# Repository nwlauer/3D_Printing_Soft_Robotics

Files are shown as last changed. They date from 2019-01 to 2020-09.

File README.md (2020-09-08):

# 3D Printing Soft Robotics

  This project revolves mostly around the fabrication of a soft robotic system out of a flexible filament that requires no post processing after printing. Additionally, a new design is constructed for a worm-like robot and accompanying control system.
  
   [Instructable](http://www.instructables.com/id/How-to-Make-a-Robotic-Worm/)
  
### Credit to Others Doing similar projects

 / [Mikey77 Instructables](http://www.instructables.com/member/mikey77/)
 / [Whitesides Research Group](http://gmwgroup.harvard.edu/research/index.php?page=23)
 / [Umburry](https://umburry.com/)
 /

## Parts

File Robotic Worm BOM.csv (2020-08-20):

Description/ID | Quantity | Qty_Unit | Manufacturer | Product No. | Source Link | Unit Cost | Notes | Type
Arduino Uno R3 | 1 | - | Elegoo | EL-CB-001 | https://www.amazon.com/ELEGOO-Board-ATmega328P-ATMEGA16U2-Compliant/dp/B01EWOE0UU | $12.98 | - | Electronic
NinjaFlex | 25 | grams | NinjaTek | - | https://www.amazon.com/NinjaTek-3DNF08117505-NinjaFlex-Filament-TPE-5kg/dp/B00J12HGDW | $0.09 | If using alternatives try to get one with similar elongation and shore hardness | Hardware&Materials
PVA | 25 | grams | SainSmart | - | https://www.amazon.com/gp/product/B00SSXAET8/ref=ppx_yo_dt_b_asin_title_o08_s00?ie=UTF8&psc=1 | $0.06 | Any Brand is fine | Hardware&Materials
2mm ID x 4mm OD Silicone Tubing | 5 | ft | Generic | - | https://www.amazon.com/DERPIPE-Silicone-Tubing-Flexible-Homebrewing/dp/B07PZT7FC7 | $0.70 | - | Hardware&Materials
4mm ID x 6mm OD Silicone Tubing | 1 | ft | Generic | - | https://www.amazon.com/dp/B08BR8MQSR | $1.20 | - | Hardware&Materials
12V Mini Diaphragm Pump | 1 | - | Parker/Hargraves | C 183-22-01 | https://www.ebay.com/itm/Mini-Diaphragm-single-head-Air-And-Gas-Hargraves-Pump-2-5L-min-12VDC/301748351096 | $22.49 | Ubiquitous on the secondary market look for deals. Similar pumps can be used in place. | Electronic
6 V 2 position 3 way mini solenoid valve | 6 |  | Zonhen | ZHV-0519 | https://www.ebay.com/itm/DC-5V-6V-2-Position-3-Way-Micro-Mini-Electric-Solenoid-Valve-for-Gas-Air-Pump/263807376340 | $2.45 | Ubiquitous on secondary market, does not have to be Zonhen brand. Usually marketed for use in eye massagers. | Electronic
12V 2A Power Supply | 1 | - | Generic | - | https://www.amazon.com/100-240V-Transformers-Switching-Applications-Connectors/dp/B077PW5JC3 | $5.00 | - | Electronic
LM2596 adjustable buck converter module | 1 | - | Generic | - | https://www.amazon.com/MCIGICM-step-down-Converter-3-0-40V-1-5-35V/dp/B06XZ1DKF2 | $2.00 | - | Electronic
1k Ohm Resistor | 7 | - | Generic | - |  | $0.01 | - | Electronic
NPN Amplifier Transistor | 6 | - | Generic | BC337 | https://www.sparkfun.com/products/13689 | $0.50 | - | Electronic
Darlington Transistor | 1 | - | Generic | TIP 120 | https://www.amazon.com/TIP120-Darlington-Transistor-Arduino-Diodes/dp/B00FVLGYEY | $1.00 | - | Electronic
Clamping Diodes | 7 | - | Generic | 1N4007 | https://www.amazon.com/ILS-Pieces-Rectifier-Component-Projects/dp/B07PXV4F2C?s=electronics | $0.01 | Can use 1N4001 and up | Electronic
XH-2A Connectors | 6 | - | Generic | - | https://www.amazon.com/IZOKEE-460pcs-Connector-Housing-Terminal/dp/B0791DJMW9?s=electronics | $0.02 | Optional for connecting the solenoid valves to the circuit | Electronic
XH-4A Connector | 1 | - | Generic | - | https://www.amazon.com/IZOKEE-460pcs-Connector-Housing-Terminal/dp/B0791DJMW9?s=electronics | $0.02 | Optional for connecting the pump | Electronic
No Residue Tap | 1 | ft | Generic | - | - | $1.00 | Any kind will do, I used Kapton | Hardware&Materials
Small Zip Ties | 6 | - | Generic | - | https://www.amazon.com/TR-Industrial-TR88301-Multi-Purpose-Cable/dp/B01018DB2E?s=electronics | $0.50 | Less then 2mm width works best | Hardware&Materials
Vinyl, Fabric & Plastic Flexible Adhesive | 2 | Ounce | Loctite | 1360694 | https://www.amazon.com/Loctite-Plastic-Adhesive-1-Ounce-1360694/dp/B001F7E9VI | $2.94 | - | Hardware&Materials
Jumper Wires | 40 | - | - | - | - | $5.00 | For Breadboarding or proto-boarding | Hardware&Materials
3D Printer | 1 | - | - | - | - | - | Must be able to print NinjaFlex | Tools
Wire Cutters and Strippers | - | - | - | - | - | - | - | Tools
Soldering Iron and Solder | - | - | - | - | - | - | Optional | Tools
Breadboard | - | - | - | - | - | - | - | Tools
Straight Pick | - | - | - | - | - | - | - | Tools

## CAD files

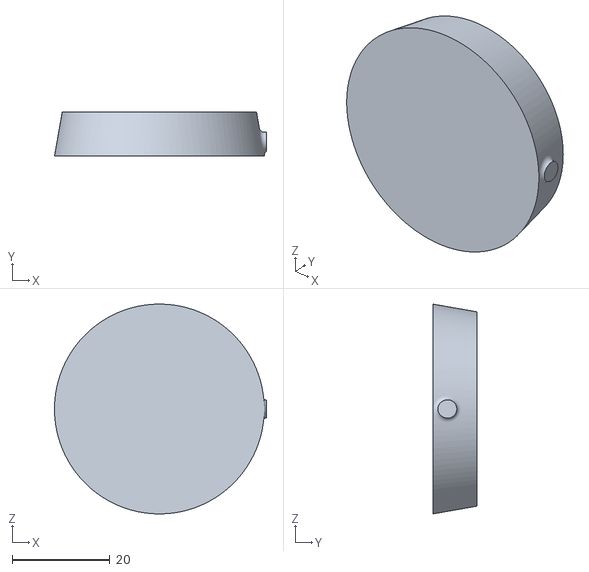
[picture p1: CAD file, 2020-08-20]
support-insert-01-offset.stl
43.4 x 9.00 x 42.9

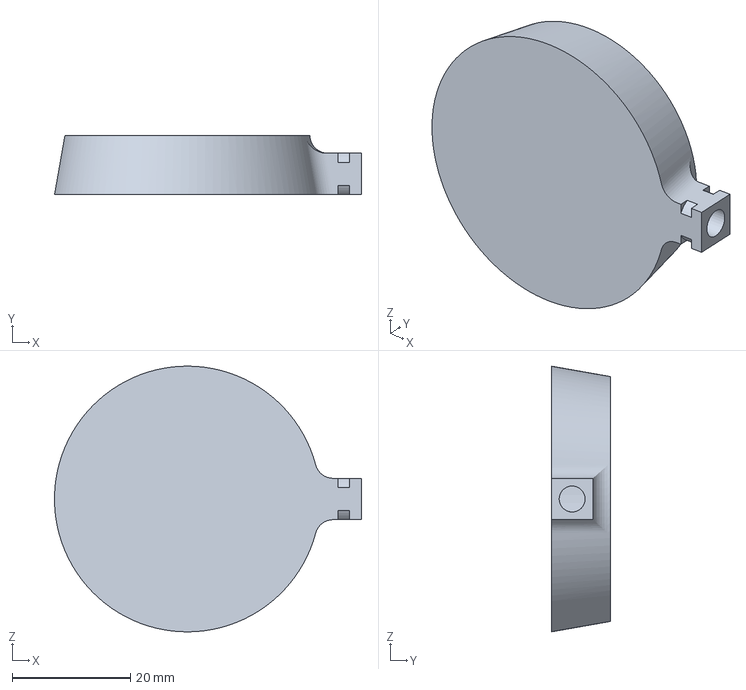
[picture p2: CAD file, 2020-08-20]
amf_file_for_mk2s (2).amf
52.0 x 10.0 x 45.0 mm

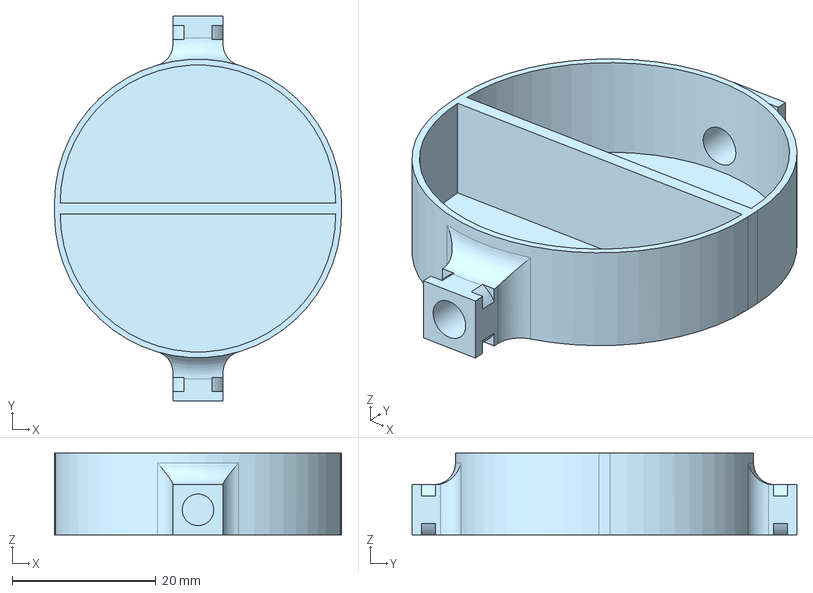
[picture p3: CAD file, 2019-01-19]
Pillow Actuator Bottom.step
40.0 x 53.6 x 11.4 mm

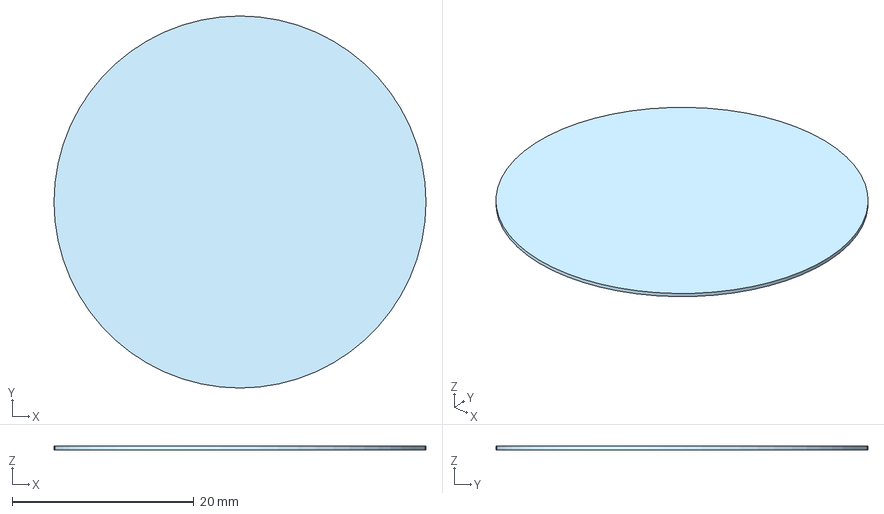
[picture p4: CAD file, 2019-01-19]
Pillow Actuator Top.step
41.0 x 41.0 x 0.4 mm

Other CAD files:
pillow-actuator-v2 (1).stl
Pillow Actuator Bottom.stl
Pillow Actuator Top.stl
pillow-actuator-v2.f3d

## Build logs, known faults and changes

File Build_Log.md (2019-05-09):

### Progress

(Jan. 15th, 2019)

It has been a while since I did an update, quite a bit has happened.

I decided to stick with the soldering iron method of creating the actuator for prototyping, in the future if it works I would like to work on creating a tool to do this with geometry to melt the specific locations of the actuator. 

Working on better settings for the top portion I found that while the rectilinear infill had the tendency to have gaps seen below, even when the outline overlap setting was increased. 

Rect

When doing infill there is a minimum line length for filling the part, the default for my printer in simplify3d was 2 mm. The circular geometry there is a line length less than 2 mm at the edges of the circle, the obvious solution would be to decrease this number until you get a solid infill. I, however, I found a better solution to be switching to a concentric infill which eliminates the issue at the edge of the circle and moves it to the center where the concentric circle to fill the center has a circumference less than 2mm, however I found that since I was over extruding and had the nozzle down further than normal it would completely fill in the center. The results of this change are bellow.

Conc

A new issue arises when the print finished, and a blob would be left in the center and the nozzle would smear over the top of the part when returning to its home position. I solved this adding some code to the end script to retract some and lift the z 10 mm. 

```
G92 E0 ; reset extruder distance
G1 E-1 F500 ; Retract 1 mm
G92 Z0 ; Relative Position Z
G1 Z10 ; Raise Z 10 mm
```

I have included my FFF process settings in the project folder for reference.

I used Loctite flexible adhesive to bond together the actuators. I only realized after that the location of the adhered portion should be closer to the center of the actuator so there can be the maximum amount of movement upon actuation.

PartialBuild

Additionally, I got two mini pumps from eBay, they are parker BLDC diaphragm pumps with feedback. Unfortunately, I accidentally shorted out one hooking it up to the power supply since I was using exposed alligator clips, I am now only using the covered type to avoid this again. I have a metro express board and some circuit python code to feed a PWM signal to the speed control pin on the motor but want to wait until I order another one before I try it, so I always have one working in reserve.

```
import board
import pulseio
from analogio import AnalogIn

analog_in = AnalogIn(board.A1) #Initialize AnalogIn
 
def duty_cycle_value(pin): #Get data from potentiometer
    return pin.value

pump = pulseio.PWMOut(board.D13, frequency=15000, duty_cycle=0) # Initialize Pump PWM. Frequency from pump data sheet

while True:
    pump.duty_cycle = duty_cycle_value(analog_in) # Loop PWM signal with duty cycle defined by pot value
```

Next, I want to design a manifold and order some solenoid valves for control.

(Sept. 18th, 2018)

I worked a bit on a new actuator design for a eventual soft robotic worm design I am working on. The design was a pillow type actuator as seen below. 

[Onshape Design](https://cad.onshape.com/documents/3c669edf96e152dec33955a7/w/b0888245c5fd9d2512150394/e/fc91afc5c4801dd98c8136da)

The first print failed due to the flexible filament not being able to bridge the distance across the actuator. This print did however show a strong bottom layer. 

FirstTry

FirstTry2

Instead of dialing in speeds and temperature to possibly allow the required bridging, I moved forward to the next design which split the actuator into two halves and also adjusted the size of the tubing hole as the previous version was a bit too small. The resulting design and print is seen below.

SecondTry1

SecondTry2

The print failed much like the one before but to a lesser extent. The higher temperature resulted in some more heavy stringing however this stinging makes me think that maybe running the top layer at travel speeds might produce better results, never the less I think adding two additional layers on top should produce a airtight top. 

After seeing the failed prints before which were just the bottom layer, I had the idea of trying to take those and weld them to the top of the actuator to possibly make a functioning one. I used a soldering iron to melt around the circumference of the top and it seemed to work as seen below. The center separator was a bit hard to weld but I am not sure of the wall's ability to hold air itself, I will try making it thicker in future iterations. 

WeldedActuator

ASIDE: During the printing of the second actuator the printer stopped extruding at a usual layer height that it has done before with other actuators. I had previously never found a definite fix for this, however thinking about the repeatability, it seemed to happen when it started printing the perimeter layers and I figured a possible mode of failure was speed and the hot end not being able to keep up with the amount of material being extruded, I tested this by increasing the temperature and lowering the speed slightly, this seemed to work, but time will tell weather this is a solid fix for this problem or just a fluke.

---------------------------------------
(Sept. 10th, 2018)

After attempting to print the adapter described in the previous post, I was unable to get a quality print with a center hole even at .1 mm layer height, while I could try a smaller nozzle and possible achieve success I decided to go back to the drawing board and try a different approach and a more simple one at that. Instead of an external adapter I decided on an internal adapter that fits completely in the larger tube and around the smaller one. This eliminates the issues of trying to print small enough to insert into the 1/8" ID on the inner tube, instead the limiting dimension on this design is the outer diameter of the smaller tube. This design also allows for faster new iterations adjusting the tolerances because of the simply design. 

After a moderately embarrassingly mistake where I used the diameter dimension instead of the radius when revolving the part, I got a functional adapter seen below. This worked however testing it on the diaphragm pump with the soft robot turned out to come close to stalling the pump and unfortunately my power supply tops out at a bit over 1 and a half amps. 

Tubing

Links:

[Thingiverse](https://www.thingiverse.com/thing:3095760)
[On-Shape](https://cad.onshape.com/documents/92cfda232b528470463f2aaa/w/1ba712666e28d8060b0fa5f9/e/f20b0e49f8c2d650ff1c5602)

Later however I realized I have a bicycle pump which I thought might be worth a try and it worked great. I will now add a electronic piston to the list of sub projects to run the robot. 

---------------------------------------------------------------------------------

(August 26th, 2018)

I got hold of a larger diaphragm pump that should be able to provide the pressure I need to cause maximum deflection or at least more deflection then I have been getting with the peristaltic pumps. The pump is made for larger tubing and doesn't fit the actuators so I had to model an adapter, I chose to make it parametric so I can change it to connect different sized tubing in the future if I need to and put the design on thingiverse. 

Thingiverse Link

[ThingiverseLink](http://www.thingiverse.com/thing:3069449)

On-Shape Link to Customizable Adapter: 

[OnshapeLink](http://cad.onshape.com/documents/9ce4cfa03e624a2dd4b5f2d3/w/101f37edd98fbd5f7c71c180/e/683bc8de0e68daec63e576c4)

----------------------------------------------------------------------------

(August 6th, 2018)

I am currently working on an enclosure for my printer which has delayed this project progress slightly, but I wanted to detail some of the design parameters that have worked so far as well as some of my plans for testing in the future. 

The main parameter I have become confident in is the wall thickness which is 2 perimeters optimally roughly with a roughly .45 millimeter, as far as top and bottom thickness between 4 and 6 layers of .2 mm work well, less leads to holes still present in the top surface which air can escape and more leads to a much stiffer actuator that won’t extend well. Channel thickness is something I would still like to experiment with more especially with different designs. For the most part I use around 1.2 mm for the design however the actual thickness is closer to 1mm because of the over extrusion in the sidewalls. 

Below are some pictures of the settings I used in Simplify3D for the actual configurations feel free to contact me, however I think there are not useful for anything other than reference because of the sensitivity of the process and the variability between printers with extrusion, actual layer height, extruder design, etc..

Process Settings 1

Process Settings 2

I would like to cover the following going forward

1. New design (pneunet approach)

2. Design of experiments with channel thickness 

3. Simulations with SOFA Framework

----------------------------------------------------------------------------------

(July 12, 2018)

I think the main point of leakage at this point is from the interface between the Vinyl tubing and the 3D print, I have confirmed this some by lengthening the entryway for the tubing as seen bellow and had some success as seen, next I would like to work on an adapter and modeling the ribs between the adapter and entry point to be a close fit. The current version of the actuator can be seen [here](https://cad.onshape.com/documents/02b6b1a719bd819477cb40a7/w/13e82c7ddb63d8f5073c5366/e/bbfd169c50e79385daa16018). 

Gif

------------------------------------------------------------------------------------------------


Original trials were made to heat the actuators in the oven after printing which while still considered post processing the print is minimal when compared to other techniques (dipping in sealant). Later in printing it was found that this process was unneeded as I was getting reasonably air tight actuators in just increasing the extrusion multiplier (1.5 to 2) depending on printer and filament. I have been able to get away with two perimeters and still create a good actuator, the top and bottom layers must be a bit more, however this may be a limit of the design having the walls so close together and the slicer having trouble getting good solid infill. 
Messy Robots

---------------------------------------------------------------------
(August 2017)
I recently just finished a 3D Printed biomimetic flower. The main purpose of this project was to get more familiar with the capabilities of straight 3D Printed pneumatic artificial muscles. While much has been done as far as 3D printing the molds and casting the muscles in silicon or some other curing elastomer not much has been done on direct 3D printing of them. Ultimately, I think there is a ways to go but direct Manufacturing the parts instead of the mold had its benefits (One solid piece, more detail and control, and ease of the process itself). Currently it seems to be limited as far as FDM printers because of the inevitable micro holes in the final print, the way this was solved by mikey77(See link in credit) using flexible sealant, while this still introduces an additional step in manufacturing I think it is better than molding in its simplicity. I still want to attempt to solve these holes by baking the printed parts hopefully allowing flow and closure of the micro-holes. Further work has been done by different people but none with results that I am seeking.

[Flower](https://imgur.com/EfdkGky)

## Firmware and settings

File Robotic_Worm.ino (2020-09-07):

//Robotic Worm By Nicholas Lauer 8-26-2020
//Last Updated 8-26-2020
// This Program controls solenoid sequencing for a soft robotic worm.
// Documentation can be found at github.com/nwlauer/3D_Printing_Soft_Robotics
//Defining Pins. Sone is the for the first solenid valve connected to the head of the robot

int Sone = 2; // Solenoid One
int Stwo = 3; // Solenoid Two
int Sthree = 4; // Solenoid Three
int Sfour = 5; // Solenoid Four
int Sfive = 6; // Solenoid Five
int Ssix = 7; // Solenoid Six
int Pump = 12; // Pump Pin
int Segd = 90; // Segment Delay: The time delay in between each segment activation
int Sqd = 500; // Sequence Delay: The time delay between each full sequence

void setup() {
  // initialize outputs
  pinMode(Sone, OUTPUT);
  pinMode(Pump, OUTPUT);
  pinMode(Stwo, OUTPUT);
  pinMode(Sthree, OUTPUT);
  pinMode(Sfour, OUTPUT);
  pinMode(Sfive, OUTPUT);
  pinMode(Ssix, OUTPUT);
}

// the loop function runs over and over again forever
void loop() {
  digitalWrite(Pump, HIGH);    // Turn Pump On
  digitalWrite(Ssix,LOW);      // Turn solenoid six off
  digitalWrite(Sone, HIGH);    // Turn solenid one on
  delay(Segd);                 // Wait for segment delay
  digitalWrite(Sone, LOW);    // Turn solenoid one off
  digitalWrite(Stwo, HIGH);    // Turn solenoid two on
  delay(Segd);
  digitalWrite(Stwo,LOW);
  digitalWrite(Sthree,HIGH);
  delay(Segd);
  digitalWrite(Sthree,LOW);
  digitalWrite(Sfour,HIGH);
  delay(Segd);
  digitalWrite(Sfour,LOW);
  digitalWrite(Sfive,HIGH);
  delay(Segd);
  digitalWrite(Sfive,LOW);
  digitalWrite(Ssix,HIGH);
  delay(Sqd);                 //Delay for Sequence Delay
}

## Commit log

2019-01-18 Added BOM
    [Soft Robotics BOM.xlsx]
2019-01-19 Added Pillow Actuator STL & STEP Files
    [Pillow Actuator Bottom.step, Pillow Actuator Bottom.stl, Pillow Actuator Top.step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]
2020-08-19 Electrical Schematics
    Schematics for the control and power circuit. KiCad
2020-08-24 Bill Of Materials
    Added Bill of Materials
    [Robotic Worm BOM.csv, Robotic Worm BOM.ods]
2020-09-07 KiCad Electronics Files
2020-09-07 Bill of Materials
    [Robotic Worm BOM.csv]
2020-09-07 Arduino Code
